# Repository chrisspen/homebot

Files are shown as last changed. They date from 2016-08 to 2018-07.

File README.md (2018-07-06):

Homebot
============================================================

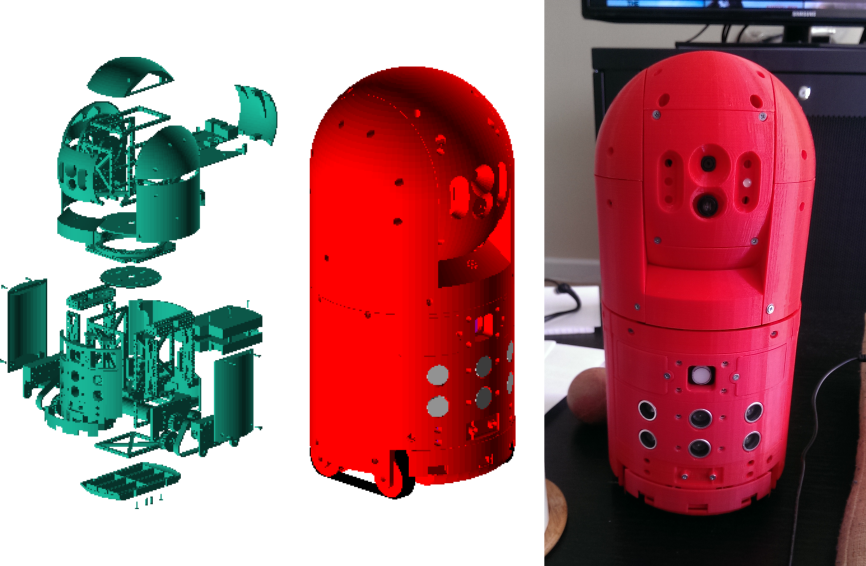
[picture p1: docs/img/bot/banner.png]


Homebot is a low cost open source robot designed for research and experimentation with [ROS](http://www.ros.org/).

Basic features include:

* head that can rotate 360 degrees horizontally and 180 degrees vertically
* monocular camera fitting with a laser ranger finder
* IMU with magnetic compass for navigation
* ultrasonic range finders and IR distance sensor for forward obstacle and cliff detection
* Raspberry Pi 3 for running ROS and high-level control
* charging dock

Demo:

[Undocking And Docking](https://youtu.be/g7_KL-V0nWs)

Shortcuts:

To deploy all code changes to the production robot, run:

    fab prod deploy.push

To just quickly push up Python code changes, run:

    fab prod homebot.deploy_code

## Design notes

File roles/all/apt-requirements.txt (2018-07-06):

# Install with:
# fab local packager.install_apt:roles/all/apt-requirements.txt

# Python
python-dev
python-pip
python-virtualenv

dphys-swapfile
#linux-firmware#not found on raspbian?
openssh-server
network-manager
wireless-tools
rsync

# Debugging helpers.
htop
curl
screen
git

# Needed by numpy/scipy
libatlas-base-dev
gcc
gfortran
g++
libblas-dev
liblapack-dev
gfortran

# Speech output.
espeak
alsa-utils
mpg321
lame

# Needed by cv2.
libgles2-mesa
libgles2-mesa-dev

# Needed by some packages that are built from source.
python-wstool
python-rosdep
ninja-build

# Needed by tf/robot-state-publisher.
libtf2-*

#ros-kinetic-robot-upstart

# Needed by Arduino firmware.
arduino-mk

# Needed by teleop and raspicam.
ros-kinetic-image-view
ros-kinetic-xacro
ros-kinetic-robot-state-publisher
ros-kinetic-rospy
ros-kinetic-compressed-image-transport
#libcamera-info-manager0d
#libcamera-info-manager-dev
ros-kinetic-camera-info-manager
libopencv-calib3d-dev

# Needed by homebot_description.
ros-kinetic-diagnostics
#ros-kinetic-diagnostics-msgs
ros-kinetic-robot-model

# Needed for raspicam
g++-arm-linux-gnueabihf

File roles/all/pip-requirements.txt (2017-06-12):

burlap==0.9.2

# Allows us to create GTK3 applications.
pgi==0.0.11.1

# head_arduino_tester
pyserial==3.2.1
#urwid==1.3.1

catkin-pkg==0.2.10

# Needed by system_node.py
# Note, large packages like scipy/numpy take forever to build on the RPi,
# so we install via the --only-binary option. However, the available versions
# with this option are limited, so we don't specify version.
#scipy==0.19.0
scipy
humanize==0.5.1
#numpy==1.12.0
numpy

#Fabric==1.10.2
#PyYAML==3.11
#burlap

#DEPRECATED: Installed by ROS?
#wiringpi2==1.1.1

Pillow==2.3.0
picamera==1.10

pint==0.7.2

# Required by ros_homebot_lrf.
#laser_range_finder
#-e git://github.com/chrisspen/laser-range-finder.git#egg=laser_range_finder

# Needed for ROS message generation.
empy==3.3.2

defusedxml
rospkg

# Teleop
Django==1.9.2
-e git://github.com/chrisspen/gevent-socketio.git#egg=gevent-socketio

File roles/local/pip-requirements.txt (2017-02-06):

# Needed by imu_visualizer.py.
vispy==0.4.0

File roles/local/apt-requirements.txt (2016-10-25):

# Needed by imu_visualizer.py.
libglfw3*

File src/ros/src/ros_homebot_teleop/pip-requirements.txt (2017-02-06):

Django==1.10.5
#gevent-socketio==0.3.6
#-e git+https://github.com/abourget/gevent-socketio.git#egg=gevent_socketio-dev
-e git://github.com/chrisspen/gevent-socketio.git#egg=gevent-socketio

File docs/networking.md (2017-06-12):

Networking
==========

Both wired and wireless connections are managed by Network Manager.

The wired connection will automatically be enabled when an ethernet cable is connected.

Wireless requires some setup, requiring an initial wired connection. Attached an ethernet cable and then confirm you can SSH in via:

    fab prod shell

Exit the shell, and setup the wireless connection by running:

    fab prod nm.add_wifi_connection:<SSID>,<PASSPHRASE>

If you get an error saying " No network with SSID '<SSID>' found." then list all available wireless networks by running:

    nmcli dev wifi list

If none are listed, then that indicates there might be a problem with the wireless driver.

Ensure all your packages and firmware is up-to-date by following [these instructions](https://raspberrypi.stackexchange.com/questions/44253/raspberry-pi-3-isnt-finding-wifi-networks).

    sudo apt-get update
    sudo apt-get upgrade
    sudo apt-get dist-upgrade
    sudo rpi-update
    sudo reboot

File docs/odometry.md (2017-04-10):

Odometry
========

Odometry measures the robot's translation and rotation from an arbitrary reference point. This is information necessary for planning robot movements and doing higher level actions like mapping and path planning.

Testing
-------

To confirm the robot is generating correct [odometry messages](http://docs.ros.org/api/nav_msgs/html/msg/Odometry.html), first start nodes to control the torso and visualize the robot:

    roslaunch ros_homebot_base serial_torso.launch
    roslaunch ros_homebot_description display_real.launch

Then command the motors to move foward are quarter speed using the differential format:

    rostopic pub --once /torso_arduino/motor/speed std_msgs/Int16MultiArray "{layout:{dim:[{label: '', size: 0, stride: 0}], data_offset: 0}, data:[64, 64]}"

or Twist format, which units are in meters:

    rostopic pub -1 /torso_arduino/cmd_vel geometry_msgs/Twist -- '[0.0875, 0.0, 0.0]' '[0.0, 0.0, 0.0]'

Note about speeds that the Arduino represents speed internally as an integer value between -255 to +255. A negative value is reverse. A positive value is forward. A zero value is stationary. To set speed via a Twist message, which only uses meters, the meter value has to be converted to the internal integer value. This is done in Motioncontroller.h via the `VELOCITY_TO_SPEED` ratio, which represents a conversion from a literal meter/second velocity value to a relative integer velocity value.

This value is about 728.57, and was determined by empirical measurement. However, it can vary based on nuances in the motor, motor controller, and tread friction with the ground.

To convert meters to integer value, you'd calculate `VELOCITY_TO_SPEED*METERS = SPEED`.

To convert an integer value to meters, you'd calculate `METERS = SPEED/VELOCITY_TO_SPEED`.

Since the maximum relative speed is 255, that means the maximum absolute speed is `255/728.57` = 0.35 meters/second.

Now look at the Rviz screen. If your motors are running and odometry messages are being generated correctly, you should see the robot moving forward in Rviz.

If you don't see anything, you'll need to diagnose the problem. Start by confirming odometry messages are being sent with:

    rostopic echo /torso_arduino/odom

If the robot is correctly shown to be moving, stop the robot with:

    rostopic pub --once /torso_arduino/halt std_msgs/Empty

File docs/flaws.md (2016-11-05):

Flaws
=====

This is a list of known design flaws.

1. battery charger overcharges

    If the battery pack is left connected while the robot is connected to external power, the LinkMan 2S-3S Lipo Balance Charger trickle charges the lipo until dangerously overcharged. Testing found that the 7.4V battery was overcharged to 8.9V, causing the battery to swell.
    
    Future designs should modify the recharge board to include a transistor that allows disconnecting the charger from the battery once the voltage reaches a safe storage voltage of 7.4V.
    
    This is really caused by the larger problem of our use of LiPo batteries. We're essentially trying to use the LiPo like an uninterruptible power supply, which means we try to keep the battery fully charged at all times. However, unlike Lead Acid batteries, used in most UPSes, which like to be kept fully charge, LiPo batteries tend to deterioate if kept at their full voltage for a few days.
    
    Workaround: When the robot is connected to external power, the battery should be charged to a safe storage charge of 7.4V and then removed.
    
    Effect: serious
    
2. limited expansion

    The overall footprint was kept small (15cm^2) to minimize cost and 3d printing time.
    However, even with use of small electronics, like the Arduino and Raspberry Pi, this leaves very little room for expansion and wire routing.
    
    Future designs should double this footprint.
    
    The motors and battery currently selected should still be powerful enough to actuate that size.
    
    Effect: average

3. front-panels are difficult to access

    The front panels, such as the bumper/edge sensor array, recharging dock, ultrasonic sensor array, and powerbutton, were designed as mainly a single piece, with electronics mounted behind, and then the entire assembly screwed onto the frame. This is difficult to access for maintainence because the panels can't easily be removed without also removing the wire connections to the Arduino. And in order to remove those, the head must be removed.
    
    Future designs should make enough room so wire slack can be added so the panels can be removed, or a socket used so the panel's electrical connections don't need direct wiring.
    
    Effect: average

4. battery charger discharges battery when load is off and external power is absent

    This is caused by the charger drawing current through the 3-pin balanced charging cable

    Future designs should add a diodes to ensure current only goes to the battery, back into the charger.

    Workaround: When the robot is turned off and disconnected from external power, the battery should be removed.
    
    Effect: average

5. treads lack suspension

    The treads ends are too blunt to overcome some sharp obstacles like door thresholds, without subjecting the robot to extensive shock.
    
    Future designs should raise the main idlers up, and include smaller more inset idlers, to allow suspension to dampen shocks.

    Workaround: place ballast in the bottom panels
    
    Effect: average

6. jittery head tilt

    The servo used to tilt the head up and down has considerable jittery, due to either a poor servo, or inadequate shielding along the servo control cable.
    
    Effect: average

7. inconsistent head pan reference sensor

    The sensor used to mark a centered head position is an IR sensor detecting a white reflective strip. This leads to false positives if there's considerable ambient light.
    
    Future designs should either use IR interruptor switch or hall effect sensor.
    
    Effect: minor

8. inadequate restraint in head side panels

    The two head neck struts are mechanically attached to the center head box via the servo spline on one side and a small clamp on the other. This allows for considerable play between the side head panels and the center head panels, creatign several mm of gap.
    
    Future designs should add small sliding retaining clasps, that attach to the corners of the head box and loop over the edge of the neck struts.

    Effect: minor

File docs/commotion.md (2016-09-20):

Prepare the ComMotion
---------------------

1. Mount the Commotion shield onto an Arduino, and plug the Arduino into a PC.
2. Install the i2cscanner Arduino sketch.
3. Confirm that it shows the address 0x1E (decimal 30) for the Commotion. If it does not, unplug the Arduino and change the Commotion's DIP switch to set the correct address. In my experience, most Commotion boards come configured for address 0x00 by default. Flip all DIP switches so they're closest to the numbers "1 2 3 4" to use the correct address.
4. Attach a short across the RST jumperr.

Prepare the Arduino
-------------------

1. Flash the "Arduino ISP" to the Arduino.

Upload ComMotion firmware
-------------------------

1. Use "File->Upload Using Programmer" option to upload firmware to the ComMotion through the Arduino Uno. THIS IS CRITICAL. USING THE NORMAL **UPLOAD** BUTTON WILL NOT WORK.

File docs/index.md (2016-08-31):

Introduction
============

Homebot is an affordable open source home-built robot designed for experimentation.

<span style="background-color: #FFFF00">This project is in beta status. Much of the documentation is incomplete.</span>

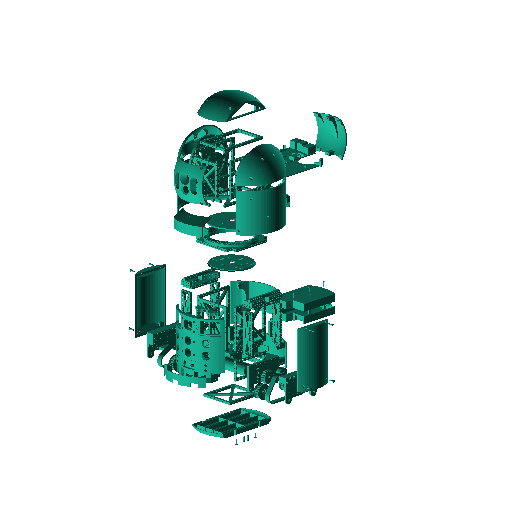
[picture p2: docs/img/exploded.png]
Exploded


#Disclaimer

This package is free software; the copyright holder gives unlimited permission to copy and/or distribute it, with or without modifications, as long as this notice is preserved. This package is distributed in the hope that it will be useful, but WITHOUT ANY WARRANTY, to the extent permitted by law; without even the implied warranty of MERCHANTABILITY or FITNESS FOR A PARTICULAR PURPOSE. Some information described herein may be potentially dangerous if misused. Follow these instructions are your own risk.

#Philosophy

This project has been constructed with the following philosophies in mind:

1. Openness
 
    There are several other "open source" robotics projects, but most only open source some of the software. Usually, large portions of the software are propreitary and most, if not all, of the hardware is proprietary. All of this project's software is open source and uses [ROS](http://www.ros.org/) as the framework. Most of the hardware is open source as well. The CAD files for all structural components are provided, and the core electronics are based on open hardware like the Raspberry Pi and Arduino. However, due to time and resource constraints, some propreitary off-the-shelf components were used.<br/><br/>

2. Modularity

    The mechanical design is based on modular components attached to a basic skeleton. Parts can be swapped out or redesigned and replaced without necessarily redesigning other components. 

#Features

The default hardware configuration is composed of:

* 1 Raspberry Pi 3 functioning as the main computer
* 2 Arudino microcontrollers for IO expansion and handling

Sensors include:

* 3 edge/cliff sensors
* 3 contact/bumper sensors
* 3 ultrasonic range finders
* 1 IMU (combined acclerometer, gyroscope and magnetometer)
* 2 microphones
* 1 5MP camera configured as a laser range finder with a functional distance of 3 meters
* 2 temperature sensors

A simple web-based user-interface is provided for operating the robot remotely and monitoring system status.

#Prerequisites

Although great effort has been made to make these instructions clear and the design as simple as possible, constructing a robot is complicated and requires a wide breadth of knowledge. This documentation assumes you have basic experience in:

* Mechanics

    You should have an understanding of basic physics, as well as how to assemble simple mechanical components. If you passed highschool physics and can assemble Ikea furniture, you should be set.<br/><br/>

* Electronics

    You should be able to read basic electricial circuit schematics, and how to wire, solder and etch simple circuit boards.<br/><br/>

* Software

    You should have an intermediate understanding of Python and C programming as well as basic network, database and Linux systems adminstration.<br/><br/>

#Onward!

1. [Allocate the appropriate tools](tools.md)
2. [Allocate the appropriate parts and supplies](parts.md)
3. [Setup your work environment](setup.md)
4. [Fabricate and assemble the hardware](hardware.md)
5. [Configure and test the software](software.md)
6. [Experiment](experiment.md)

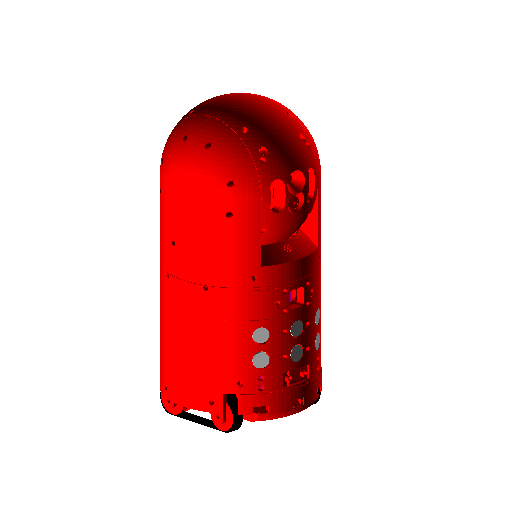
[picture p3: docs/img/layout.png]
Layout


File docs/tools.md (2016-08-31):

General
-------

To complete this project, you will need the following tools:

* a good phillips head screwdriver

    I recommend a gyroscopically controlled electric screwdriver, since it will allow fast assembly while still allowing you to regulate speed to prevent stripping.
    
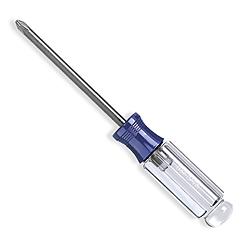
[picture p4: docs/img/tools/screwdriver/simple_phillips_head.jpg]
tool
    
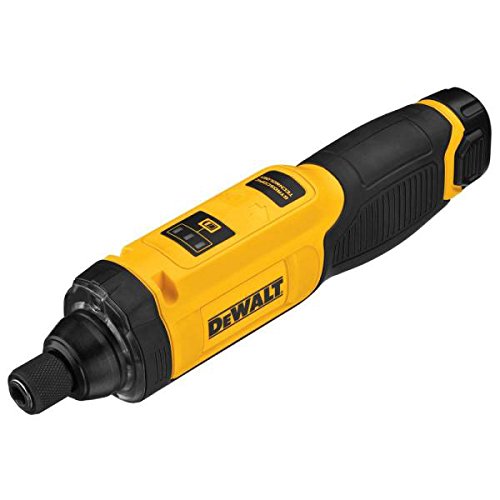
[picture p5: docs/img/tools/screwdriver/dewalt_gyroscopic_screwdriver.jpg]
tool
    
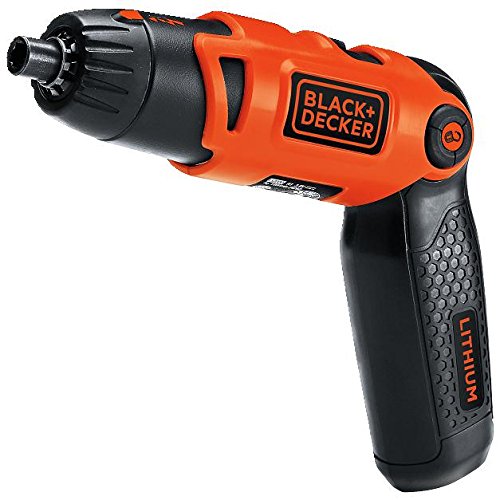
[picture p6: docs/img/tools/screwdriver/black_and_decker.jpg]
tool
    

* wire strippers

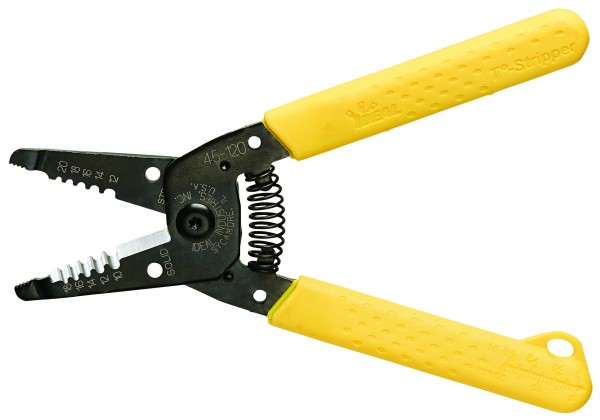
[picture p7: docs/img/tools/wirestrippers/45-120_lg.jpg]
tool
    
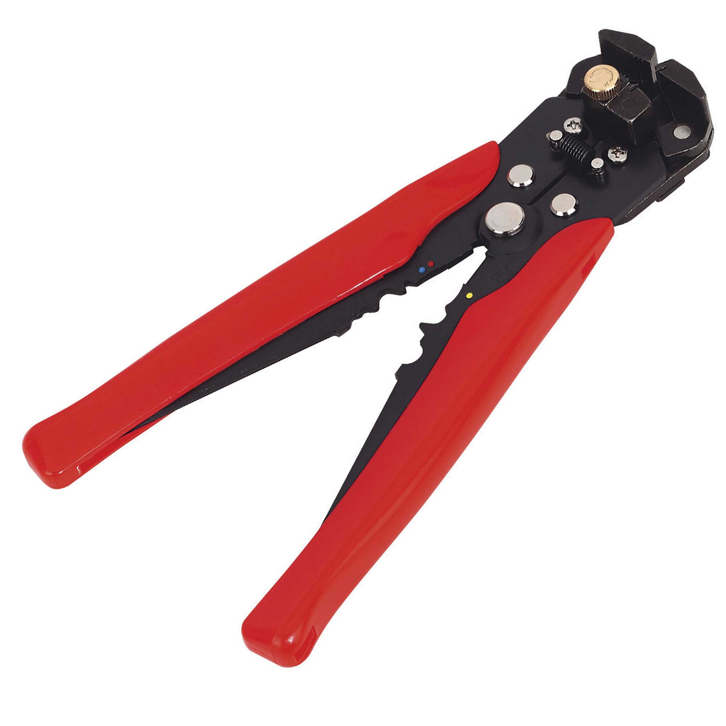
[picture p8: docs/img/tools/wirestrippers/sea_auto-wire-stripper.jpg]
tool
    

* flush wire cutter

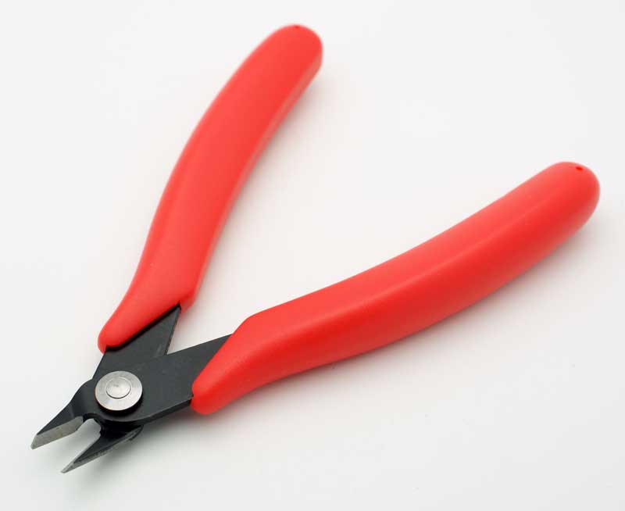
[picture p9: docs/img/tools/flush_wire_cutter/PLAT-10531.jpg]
tool
    

* exacto knife

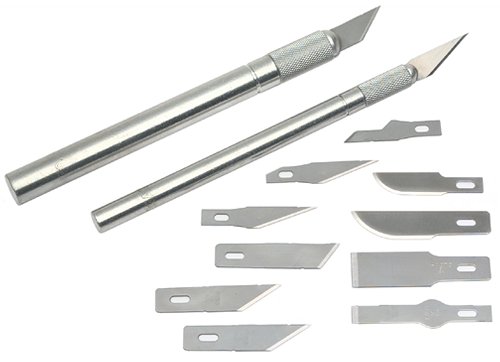
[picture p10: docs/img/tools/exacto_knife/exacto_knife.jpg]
tool
    
    
* tweezers

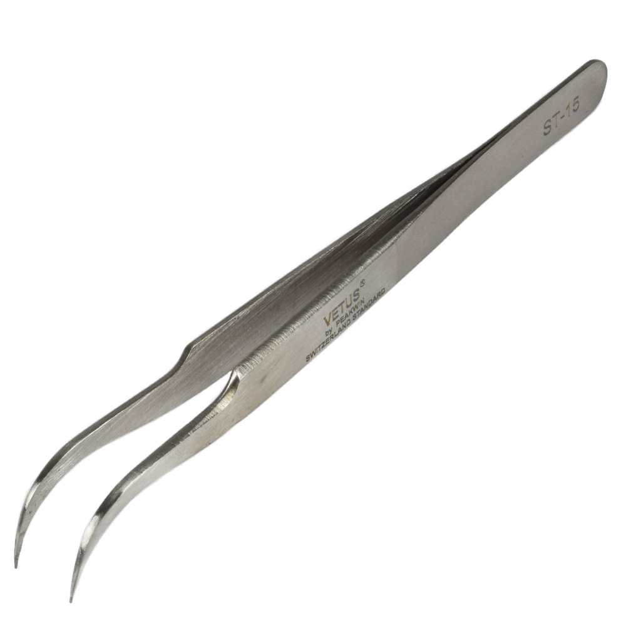
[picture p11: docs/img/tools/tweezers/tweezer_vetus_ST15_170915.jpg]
tool
    

* soldering iron

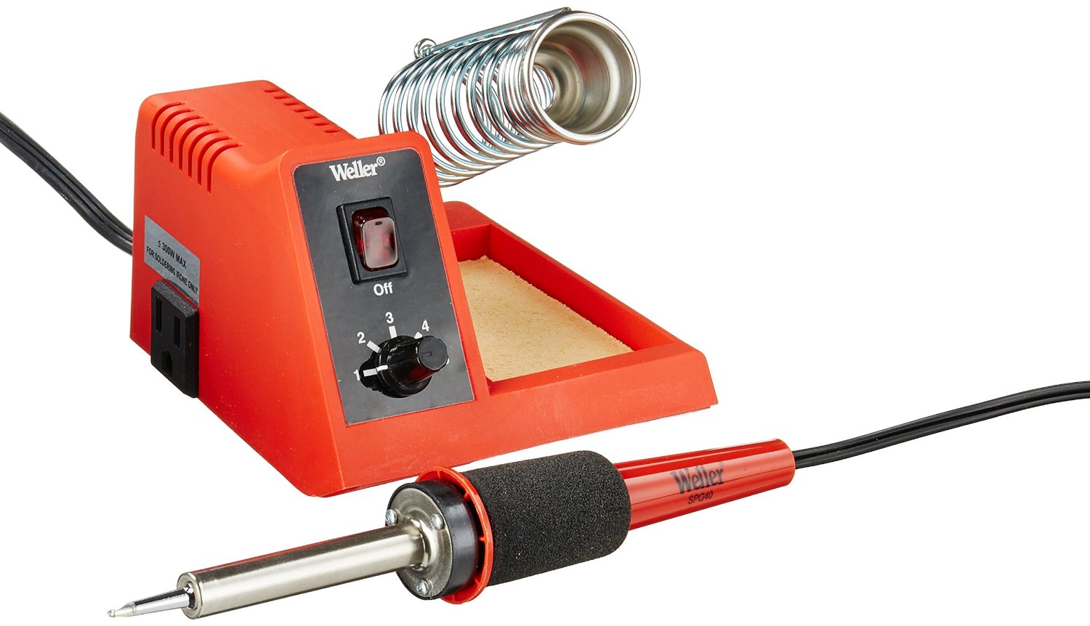
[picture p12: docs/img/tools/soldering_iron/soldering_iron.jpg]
tool
    

* helping hands

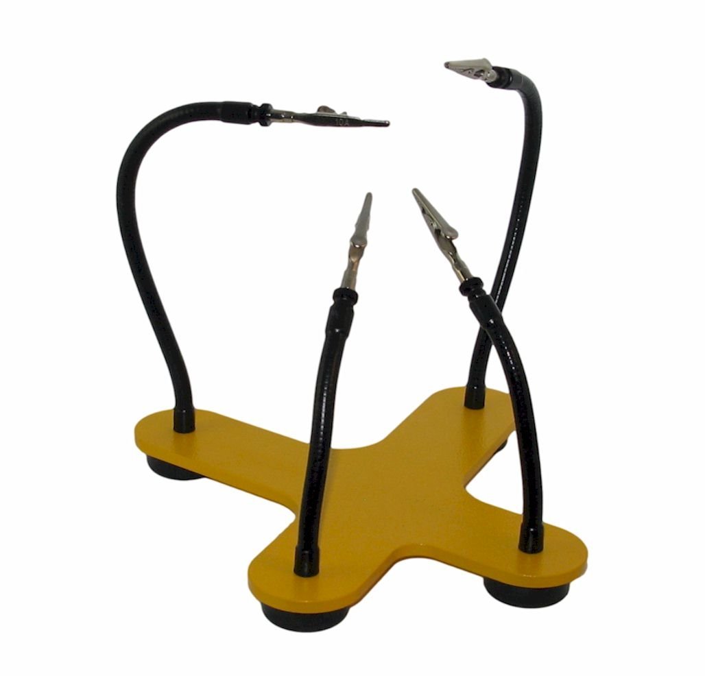
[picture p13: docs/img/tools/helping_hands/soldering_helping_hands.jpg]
tool
    

* heat gun

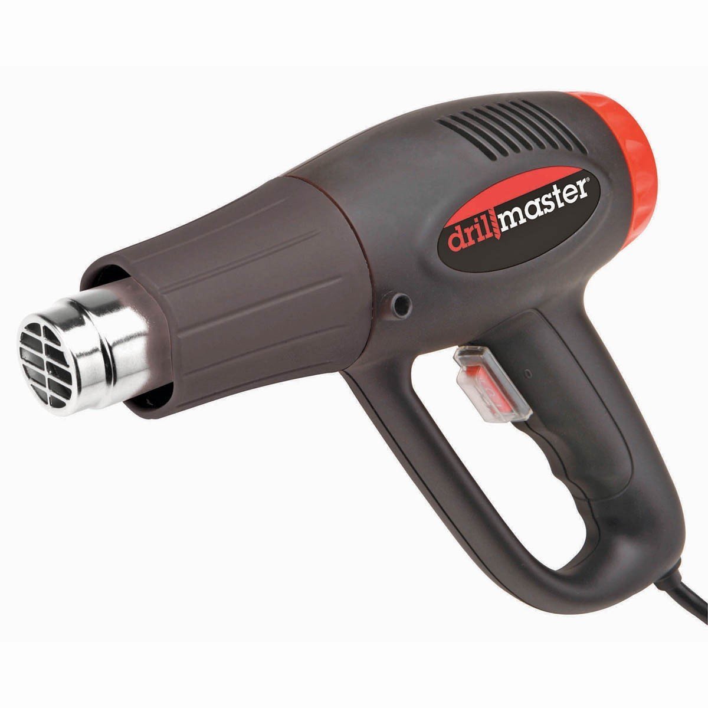
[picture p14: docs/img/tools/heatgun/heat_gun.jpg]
tool
    

3D Printing
-----------

If you want to 3D print the mechanical components yourself, you'll also need the following tools. If don't want to invest in a 3D printer, you can outsource the printing to one of many companies like [Shapeways.com](http://www.shapeways.com) or [Ponoko.com](Ponoko.com). 

* a 3d printer with a print volume of at least 15cm^3. All parts were originally developed and printed using a [Printrbot Simple Metal with heated bed](https://printrbot.com/shop/assembled-simple-metal-with-heated-bed/).

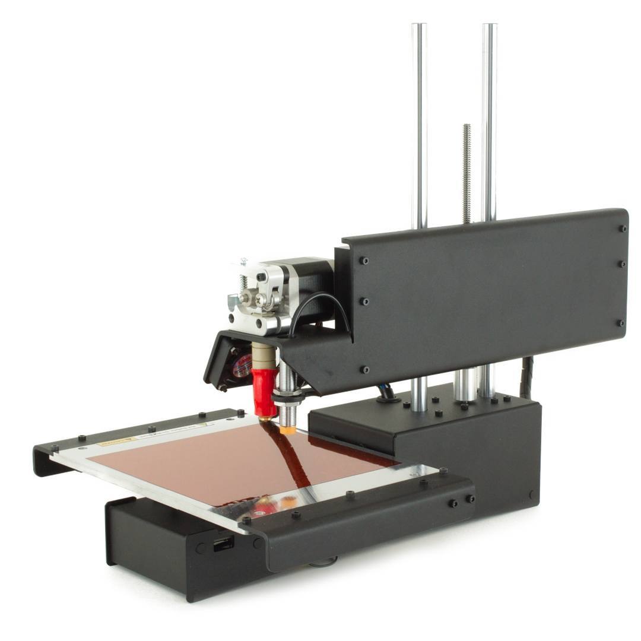
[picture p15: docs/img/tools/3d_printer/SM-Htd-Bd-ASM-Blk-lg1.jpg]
tool
    
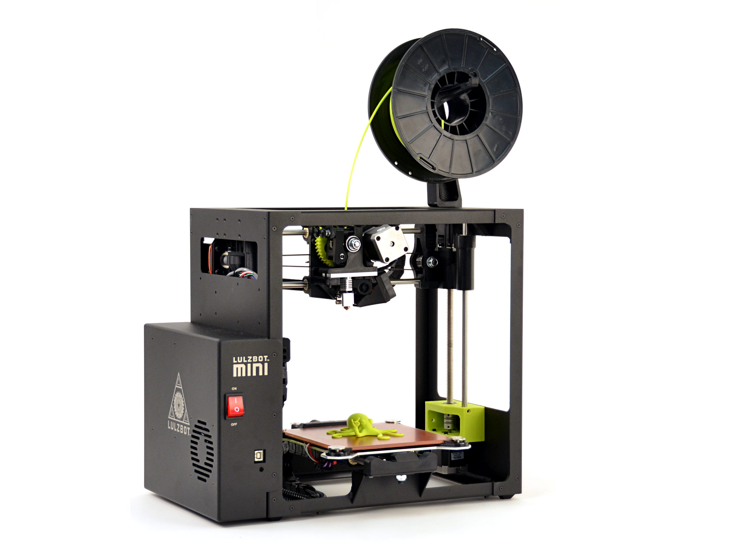
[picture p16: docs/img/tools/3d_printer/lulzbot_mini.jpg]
tool
    
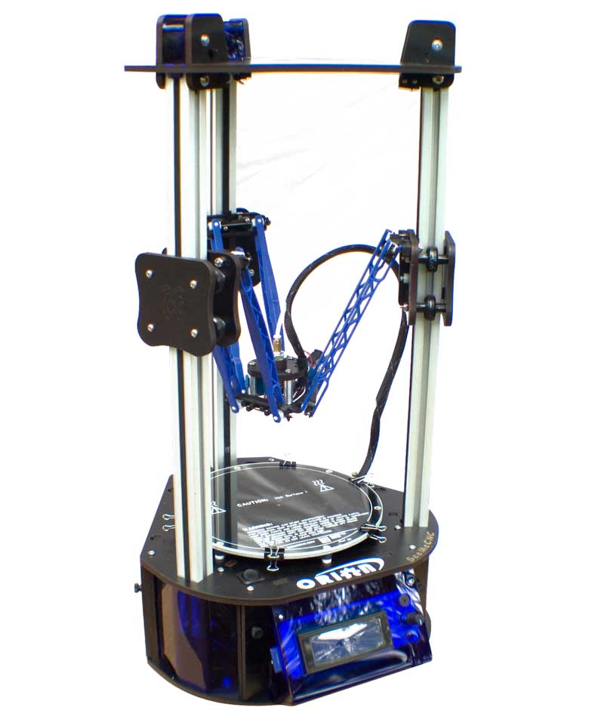
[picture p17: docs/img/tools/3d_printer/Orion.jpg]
tool
    

* 4-inch taping knife 

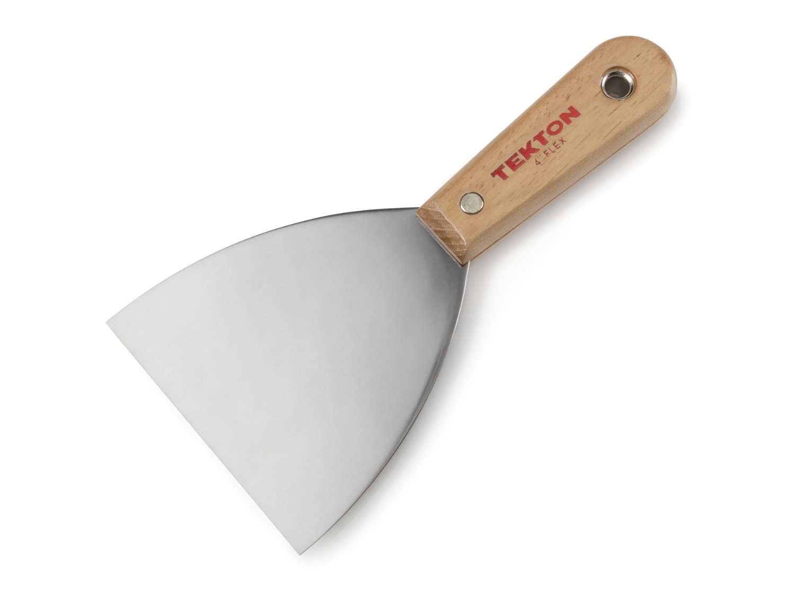
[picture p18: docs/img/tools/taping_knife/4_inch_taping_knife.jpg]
tool
    

* tapered pallet knife

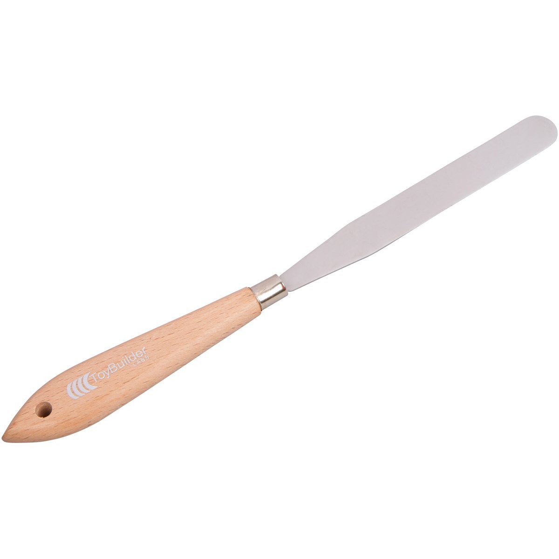
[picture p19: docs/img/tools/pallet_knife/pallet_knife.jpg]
tool
    

PCB Fabrication
---------------

If you plan to fabricate your own printed circuit boards, you'll need the additional tools.

* black and white laser printer

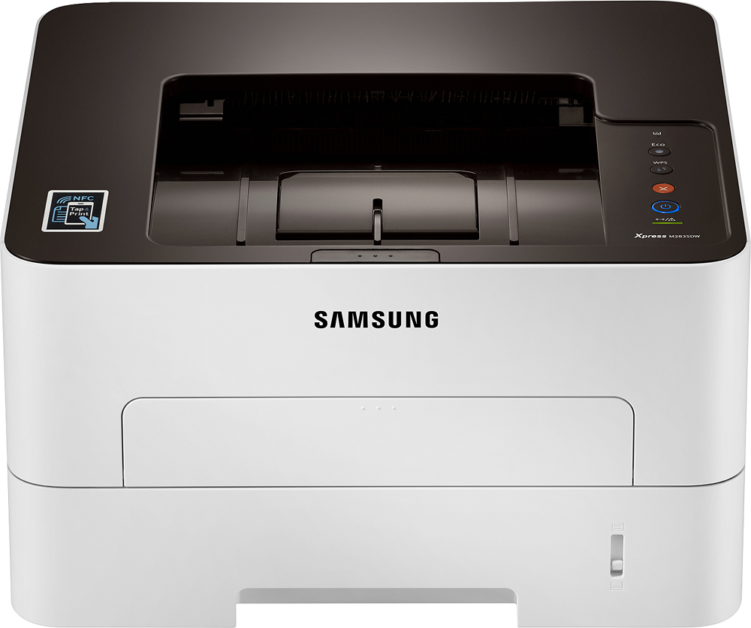
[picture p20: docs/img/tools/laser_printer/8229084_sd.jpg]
tool
    

* 1qt plastic container

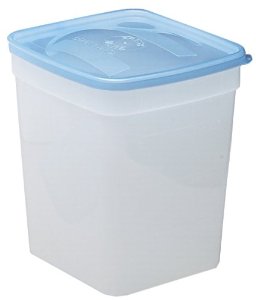
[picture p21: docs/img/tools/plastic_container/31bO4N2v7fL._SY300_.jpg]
tool
    

* air pump with bubbler

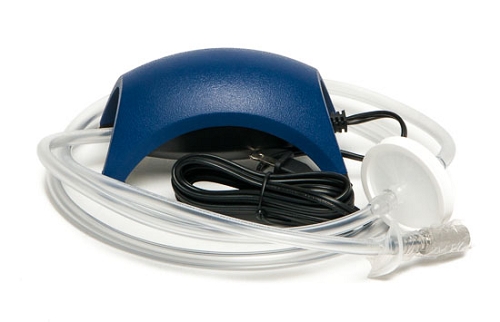
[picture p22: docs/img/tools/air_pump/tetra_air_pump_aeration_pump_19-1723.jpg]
tool
    
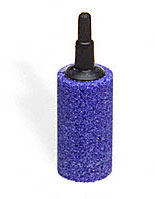
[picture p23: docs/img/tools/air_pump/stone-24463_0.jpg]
tool
    

* laminator

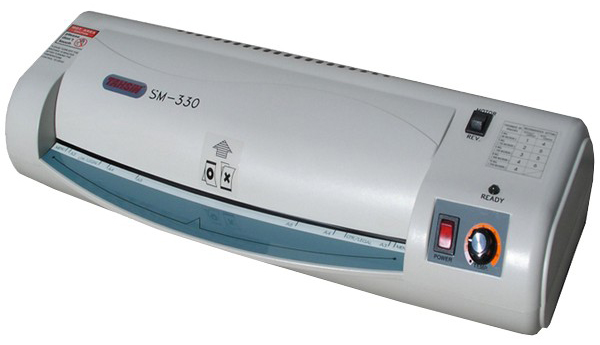
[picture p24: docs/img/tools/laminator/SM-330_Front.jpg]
tool
    

* toaster oven or reflow oven

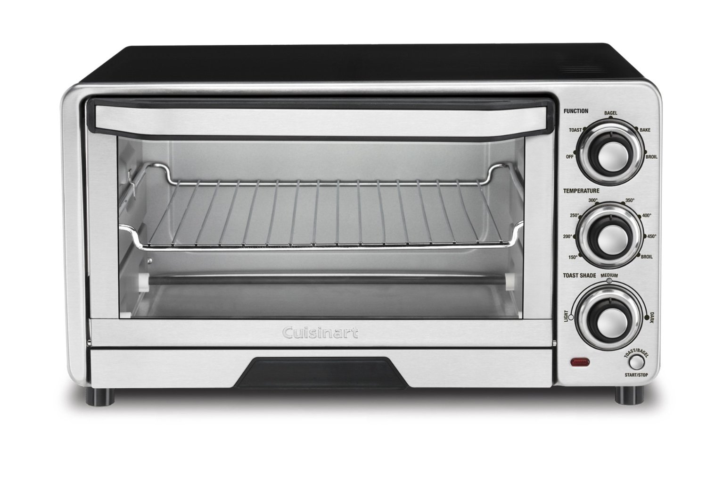
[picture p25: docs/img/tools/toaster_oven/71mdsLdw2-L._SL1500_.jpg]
tool
    
    tool

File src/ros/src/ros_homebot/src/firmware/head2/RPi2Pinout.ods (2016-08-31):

RPi2 Pin | GPIO Pin | Supports PWM | Mode | Function | Label | Wire Color | Notes
1 | 3.3V
2 | 5V
3 | I2C SDA
4 | 5V
5 | I2C SDL
6 | GND
7 | GPIO4
8 | NA
9 | GND
10 | NA
11 | GPIO17
12 | GPIO18
13 | GPIO27
14 | GND
15 | GPIO22
16 | GPIO23
17 | 3.3V
18 | GPIO24
19 | SPIO MOSI
20 | GND
21 | SPIO MISO
22 | GPIO25
23 | SPIO SCLK
24 | SPIO CS0
25 | GND
26 | SPIO CS1
27 | NA
28 | NA
29 | GPIO5
30 | GND
31 | GPIO6
32 | GPIO12
33 | GPIO13
34 | GND
35 | GPIO19
36 | GPIO16
37 | GPIO26
38 | GPIO20 |  | output | laser power | LP
39 | GND
40 | GPIO21

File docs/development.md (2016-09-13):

These are some miscellaneous notes and conventions about project development.

Creating New Messages and Actions
---------------------------------

Homebot fully supports the ROS concepts of [messages](http://wiki.ros.org/Messages), [services](http://wiki.ros.org/Services) and [actions](http://wiki.ros.org/actionlib).

Each of these is defined by a simple text file. Custom homebot-specific messages and services are defined in the ros_homebot_msgs package.

Many of the messages and services concerning the Arduino boards have been auto-generated by the ros_homebot_python package. The definitions for these are contained in `ros_homebot_python/constants.py`. If you ever add or modify this file, execute it with:

    python constants.py

Additional message and service definitions can be added to ros_homebot_msgs directly. If you do add new definitions, be sure to execute:

    python update_makelists.py

to ensure the ROS makelist contains the most recent list of messages and services to generate. Then, to rebuild all message and service objects, from the `src/ros` directory, run:

    . ./setup.bash
    catkin_make --pkg ros_homebot_msgs

Documentation Server
--------------------

To run the [documentation server](http://www.mkdocs.org/#getting-started) locally:

    mkdocs serve -a :9999

To [deploy documentation](http://www.mkdocs.org/user-guide/deploying-your-docs/), run:

    mkdocs gh-deploy --clean

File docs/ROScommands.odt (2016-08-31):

ROS Commands and Terminology

- rospack list – list all installed ROS packages
- rospack find <package-name> - find the package-name
- roscd <package-name> – change to this package’s directory (don’t need to be in the parent)
- rosls <package-name> – list the contents of the directory for this package
- roscore – start the ROS master
- node – a running instance of a program is called a node
- rosrun package-name executable-name --- start a node, rosrun doesn’t need a path to the executable; it infers the path to the executable from the package-name
- rosnode list – list all currently running nodes. Note: node names may not match the name of the executable.
- rosnode info – all sorts of useful info about the node
- rqt_graph – show the communication graph. Ovals represent nodes, arcs represent (and are labeled with) topics. Here you can see what topics are available (for publishing or subscribing) for your own programs.
- rostopic list – get a list of active topics
- rostopic echo topic-name – see the data that is being published on this topic (e.g., rostopic echo turtle1/pose)
- rostopic info topic-name – get a bunch of info about a topic. Note: first line tells the message type for the topic
- rosmsg show message-type-name – show details about the message type (i.e., show the names and data types of the components of the message).
- rostopic pub –r rate-in-hz topic-name message-type message-content – publish a message from the command line
- message type names always are of the form package-name/type-name (e.g., turtlesim/Pose)



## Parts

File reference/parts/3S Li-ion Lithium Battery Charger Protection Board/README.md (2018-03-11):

XINY 3S Li-ion Lithium Battery Charger Protection Board
=======================================================

https://www.amazon.com/XINY-Protection-Over-discharge-Overcurrent-Short-circuit/dp/B01J9BSJ80/

overcharge detection voltage :4.25 ± 0.025V(Stop charging, When 1 of 3 battery out voltage> 4.25 ± 0.025V)
over discharge detection voltage :2.50 ± 0.08V(Stop out, When 1 of 3 battery out voltage < 2.5V)
Operating Current: 15A (natural cooling 10A, additional heat sink 15A, the maximum instantaneous current of 30A)
Main features: over charge protection, over-discharge protection, short circuit protection, overcurrent protection.
No part design on the back, can be attached to the heat sink to ensure that large currents to work long hours.

Lift Condition: Protecting release the auto recovery, without activation.

Module:3S Li-ion Lithium Battery Protection Board
overcharge detection voltage :4.25 ± 0.025V
overcharge Lift the voltage:4.15 ± 0.05V
over discharge detection voltage :2.50 ± 0.08V
over discharge Lift the voltage:3.00 ± 0.1V
overcurrent current:20-30A
working current:15A(Natural cooling 10.A, add heat sink 15A, the maximum instantaneous current 30A)
Remove protection condition automatic recovery, without activation
Protections:
Short circuit protection
Overcharge protection
Over-discharge protection
Overcurrent protection
Operating temperature:-40~+85℃
Size:50*22*4mm(L*W*H)
Package include:
1 x 3S Li-ion Lithium Battery Charger Protection Board

DOES NOT BALANCE

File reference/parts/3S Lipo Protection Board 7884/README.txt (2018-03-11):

12.6V 4A 3S Dual MOS Polymer Li Battery Protection Board for 3pcs 18650
=======================================================================

http://www.icstation.com/126v-dual-polymer-battery-protection-board-3pcs-18650-p-7884.html

Icstation 12.6V 4A 3S Lithium Battery Protection PCB BMS Board With AO8810 Dual MOS for 18650 18550 Li-ion Lipo Battery Cell Pack

1. Input voltage:0-26V
2. Working temperature:-40~85℃
3. Overcharge protect voltage:4.325V-4.375V
4. Overcharge release voltage:4.1V-4.2V
5. Over discharge protect voltage:2.32V-2.48V
6. Over discharge release voltage:2.9V-3.1V
7. Overcharge protect delay time:0.5-1.5S
8. Overcharge release delay time:50-150ms
9. Over current protect delay time:0.4-1.6ms
10. Resistance: 30mohm ~ 80mohm
11. Static current:1.8-14.2uA
12. Over current:8-12A
13. Working voltage:6-12.6V

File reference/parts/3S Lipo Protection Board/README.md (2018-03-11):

Icstation 12V 8A 3S Lithium Battery Protection PCB BMS Board for 18650 18550 Li-ion Lipo Battery Cell Pack Sqaure
=================================================================================================================

https://www.amazon.com/Icstation-12V-8A-3S-Protection/dp/B01LX8M9DK/

Product Features

    12V 8A 3 cell Li-ion battery charge discharge protection board with Japan battery control IC
    Overcharge protection voltage: 4.2v±0.025v
    Over-discharge protection voltage: 2.8V±0.1V
    Continuous Working Current: 8A
    PCB size: 53 X 18 X 3mm/2.09 X 0.71 X 0.12inch(L*W*H)

Product Description
    
    This 3 cell lithium ion battery protection board is equiped with Japan battery control IC with over charging, over discharging, over current and short circuit protection.
    It is perfect for li-ion lipo battery cell pack such as 18650,18550, 14500 avoiding the damage during charging or discharge then prolong their lifetime.

Specifications:

    1. PCB size: 53 X 18 X 3mm/2.09 X 0.71 X 0.12inch(L*W*H)
    2. overcharge protection voltage: 4.2v±0.025v
    3. Over-discharge protection voltage: 2.8v±0.1v
    4. Continuous Working Current: 8A
    5. Maximum Load: 90W@12V

Package Included:

    2X 12V 8A 3S 18650 Lithium Battery Protection Board

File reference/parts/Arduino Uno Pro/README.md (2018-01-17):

Arduino Uno Pro
===============

http://www.hobbytronics.co.uk/arduino-uno-pro

https://github.com/maniacbug/mighty-1284p

Arduino UNO*Pro - Upgrade

The UNO*Pro is a simple plugin replacement for the existing ATmega328 chip (DIL socket version) and turns your existing UNO (or Duemilanove or Diecimila) into something much closer to a Mega board whilst retaining the UNO form factor and shield compatibility (see below). NOTE: Arduino main board not included.

The Arduino UNO is still the best selling Arduino board on the market, and with good reason - there are a vast range of shields available for the UNO board format.

The UNO is still a great development board, but it loses out to its big brother the Arduino Mega2560 in many areas. The Mega has 4x the flash program space, 8x as much RAM and four times as much eeprom storage space. It also has 4 serial ports and many more IO pins, but comes in a larger format and a number of shields are not compatible due to pin changes. So how can you increase the performance of the Arduino UNO? This is where the UNO*Pro upgrade board comes in.

The UNO*Pro replaces your Arduino ATmega328/168 chip with an ATmega1284 chip

Shield Compatibility
--------------------

For the most part, the UNO*Pro should be compatible with most shields designed for the Arduino UNO.

What is the same as an Arduino UNO

    All the digital pins D0 through D13
    SPI pins (SCK, MISO, MOSI)
    Analog inputs A0 - A3
    I2C pins (SDA / SCL)

What has changed

    Some of the PWM pins have changed. PWM is no longer available on D5, D6 and D11. These PWM outputs have moved to D8, D12 and D13
    Analog inputs A4 and A5 are no longer on the same pins as the I2C pins. They are now available on the extra 12 way header

NOTE: The analog-to-digital (ADC) pins seem to behave a little differently. Using digitalRead() on these pins, a higher than usual reference voltage is used, resulting in even 4V being interpreted as a logical 0. If you want to get normal behavior, you'll need to use analogRead() and then convert that 0-1024 scale to 0-1.

Also, YOU CANNOT USE ANY OF THE ANALOG PINS AS OUTPUTS. They only work as inputs.

Installation
------------

Adding the UNO*Pro board to Arduino IDE

Before you can use your new UNO*Pro, you need to add support for the ATmega1284 chip to the Arduino IDE

Arduino 1.05 or below

If you are using Arduino 1.0.5 or below then download the Arduino ATmega1284 support files below and copy the atmega1284p directory into your arduino/hardware directory.

Arduino 1.5.5 and above

If you are using Arduino 1.5.5 or later then installation is simpler.

Under the hardware/arduino/avr/variants directory create a new directory called uno_pro

    In latest latest versions of the Arduino IDE it stores its settings in a different location
    For version 1.6.12 for example it will be something like
    C:\Users\________\AppData\Local\Arduino15\packages\arduino\hardware\avr\1.6.12\

Into this directory place the file pins_arduino.h

Next, open the hardware\arduino\avr\boards.txt file with a text editor and add the following entries for the UNO*Pro board

##############################################################

uno_pro.name=Arduino Uno*Pro

uno_pro.upload.tool=avrdude
uno_pro.upload.protocol=arduino
uno_pro.upload.maximum_size=130048
uno_pro.upload.maximum_data_size=16384
uno_pro.upload.speed=115200

uno_pro.bootloader.tool=avrdude
uno_pro.bootloader.low_fuses=0xFF
uno_pro.bootloader.high_fuses=0xDE
uno_pro.bootloader.extended_fuses=0xFD
uno_pro.bootloader.unlock_bits=0x3F
uno_pro.bootloader.lock_bits=0x0F
uno_pro.bootloader.file=optiboot/optiboot_atmega1284p.hex

uno_pro.build.mcu=atmega1284p
uno_pro.build.f_cpu=16000000L
uno_pro.build.board=AVR_UNO_PRO
uno_pro.build.core=arduino
uno_pro.build.variant=uno_pro

##############################################################

Programming the new UNO*Pro

Programming your upgraded UNO*Pro board is just the same as before using the normal Arduino IDE software. The only difference is that you need to select Arduino UNO*Pro rather than Arduino Uno from the Boards menu.

Start up the Arduino IDE and select Arduino UNO*Pro.

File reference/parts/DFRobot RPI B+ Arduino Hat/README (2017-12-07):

Raspberry Pi B+ Meet Arduino Shield SKU:DFR0327

http://www.dfrobot.com/wiki/index.php?title=Raspberry_Pi_B%2B_Meet_Arduino_Shield_SKU:DFR0327

https://www.dfrobot.com/wiki/index.php/Arduino_Shield_for_Raspberry_Pi_2B_and_3B_SKU:DFR0327

Specification

    Onboard Microcontroller: ATmega32u4
    Arduino Leonardo Chip
    Arduino Compatible pin mapping
    Compatible with All arduino standard shield and sensors
    System Voltage: 5v
    Arduino Digital I/O: 20
    Arduino Analog I/O: 6
    Raspberry Pi B+ GPIO : 16
    Raspberry Pi B+ I2C: 1
    Raspberry Pi B+ ID_I2C: 1
    Raspberry Pi B+ SPI: 1
    Raspberry Pi B+ TTL UART: 1
    Dimension: 88mm x 56mm x 26mm

Note, the Pi-ID IIC pins go to the RPi pins 27/28 (ID_SD/ID_SC), which is the I2C interface for the EEPROM.

The Pi-IIC pins go to the normal I2C pins at RPi pins GPIO2 (SDA) and GPIO3 (SCL).

Note of warning. This shield appears as an I2C device at address 0x68. This shouldn't be a problem in most cases, but make sure any I2C devices you want to use with it aren't hardcoded for that same address. Otherwise they won't work. I stumbled into this problem with an I2C device that also happened to use address 0x68.

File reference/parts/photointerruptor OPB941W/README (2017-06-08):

https://www.digikey.com/product-detail/en/tt-electronics-optek-technology/OPB941W51Z/365-1234-ND/1007365

Wiring (for a GVS sensor plug):

    Connect green (gnd) and black (cathode) wires together, this will be the common ground.
    
    Add a resistor of 330 in series with red (anode). This limits the current through the IR emitter.
    
    Connect white (vcc) to the anode resistor (red). This will be +5V.
    
    Leave blue (out) as is. This will be signal out, going to a digital pin on the Arduino, configured to use a 20k pullup resistor.

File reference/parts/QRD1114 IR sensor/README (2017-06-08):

Design 1:

    Pin 1 (IR receiver output) in series with resistor 25700. (white)
    
    Pins 2 and 4 connected to ground. (black)
    
    Pin 3 (IR emitter +V) in series with resistor 330. (red)

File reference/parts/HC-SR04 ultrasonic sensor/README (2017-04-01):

HC-SR04 ultrasonic sensor

Note, even though it has two pins for Trig and Echo, these can be shorted to create a three-pin interface.

https://bitbucket.org/teckel12/arduino-new-ping/wiki/Home#!examples

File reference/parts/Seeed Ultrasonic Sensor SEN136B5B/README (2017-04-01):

Seeed Ultrasonic Sensor SEN136B5B

http://wiki.seeed.cc/Ultra_Sonic_range_measurement_module/

Features:
    
    Detecting range: 3cm-4m 

    Best in 30 degree angle 

    Electronic brick compatible interface 

    5VDC power supply 

    Breadboard friendly

    Dual transducer 

    Arduino library ready

Specifications
    
    Supply voltage  5V
    Global Current Consumption  15 mA
    Ultrasonic Frequency    40k Hz
    Maximal Range   400 cm
    Minimal Range   3 cm
    Resolution  1 cm
    Trigger Pulse Width     10 μs
    Outline Dimension   43x20x15 mm

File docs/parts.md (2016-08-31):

#Parts

A complete list of parts, estimated prices, and suggested retail links is available [here](parts.ods).

#Supplies

* 3040 3M Blue Painter's tape

* acetone

* paper towels

* 1kg of red PLA filament

* 0.5kg of black PLA filament

* 0.5kg of black Ninjaflex filament

* 60/40 solder

#PCB fabrication supplies

If you plan to fabricate your own PCB, you'll need the additional supplies.

* white vinegar

* hydrogen peroxide

* non-iodized salt

* single side FR4 copper clad board

* PCB toner transfer paper

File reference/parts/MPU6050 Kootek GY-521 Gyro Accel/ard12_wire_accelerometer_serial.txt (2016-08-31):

// This example read 14 values from an MPU-6050 digital accelerometer/gyroscope,
// using the Wire library for Arduino. It sends these values over the serial line
// to a PC.
// These values are 6 bytes acceleration measurements, 2 bytes temperature
// measurement, 6 bytes gyroscope measurements.

#include<Wire.h>

const int address=0x68;              // I2C address of the MPU-6050 accelerometer

void setup(){
  // the following lines of code init the Wire library and wake-up the accelerometer
  Wire.begin();
  Wire.beginTransmission(address);   // speak with I2C address 0x68
  Wire.write(0x6B);
  Wire.write(0);
  Wire.endTransmission(true);
  // initiate serial communication with the PC
  Serial.begin(57600);
}

void loop(){
  Wire.beginTransmission(address);
  Wire.write(0x3B);                   // starting action at register 0x3B
  Wire.endTransmission(false);

  Wire.requestFrom(address,14,true);  // request values from 14 registers (0x3B .. 0x48)
  Serial.write('#');                  // ... and send them over the serial line
  Serial.write(Wire.read());          // ACCEL_XOUT_H
  Serial.write(Wire.read());          // ACCEL_XOUT_L
  Serial.write(Wire.read());          // ACCEL_YOUT_H
  Serial.write(Wire.read());          // ACCEL_YOUT_L
  Serial.write(Wire.read());          // ACCEL_ZOUT_H
  Serial.write(Wire.read());          // ACCEL_ZOUT_L
  Serial.write(Wire.read());          // TEMP_OUT_H
  Serial.write(Wire.read());          // TEMP_OUT_L
  Serial.write(Wire.read());          // GYRO_XOUT_H
  Serial.write(Wire.read());          // GYRO_XOUT_L
  Serial.write(Wire.read());          // GYRO_YOUT_H
  Serial.write(Wire.read());          // GYRO_YOUT_L
  Serial.write(Wire.read());          // GYRO_ZOUT_H
  Serial.write(Wire.read());          // GYRO_ZOUT_L
  delay(500);                         // wait 0.5 seconds
}

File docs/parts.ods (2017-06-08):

Name | Part Number | Partial Usage | Unit Price | Quantity | Total Price | Open | Notes | URL | Alternative
CONN RCPT 5POS 5.00MM PCB SLDR | A115298-ND |  | $6.41 | 1 | $6.41 |  | battery pins | http://www.digikey.com/product-detail/en/te-connectivity-amp-connectors/5146800-1/A115298-ND/2262232
CONN HDR 5POS 5.00MM KINKED PIN | 5787446-1-ND |  | $2.98 | 1 | $2.98 |  | battery receptacle | http://www.digikey.com/product-detail/en/te-connectivity-amp-connectors/5787446-1/5787446-1-ND/1122081
Arduino Uno |  |  | $25.00 | 1 | $25.00 | 1 | torso controller | Arduino Uno
Arduino Uno Pro expansion board | UNOPRO |  | $13.00 | 1 | $13.00 |  | torso controller | http://www.hobbytronics.co.uk/arduino-uno-pro
Raspberry Pi 3 |  |  | $35.00 | 1 | $35.00 | 1 | main computer | https://www.raspberrypi.org/products/raspberry-pi-3-model-b/
ComMotion Motor Controller | RS039 |  | $45.00 | 1 | $45.00 | 0 | Discontinued. | http://www.dagurobot.com/goods.php?id=174
BMS-706MG Servo |  |  | $16.00 | 1 | $16.00 |  | head tilt actuator | http://www.hobbyking.com/hobbyking/store/__8784__BMS_706MG_Low_Profile_High_Speed_Servo_Metal_Gear_4_6kg_13sec_32g.html
Turnigy nano-tech 3000mAh 2S2P |  |  | $18.00 | 1 | $18.00 |  | main battery | http://www.hobbyking.com/hobbyking/store/__23821__Turnigy_nano_tech_3000mAh_2S2P_20_40C_Lipo_Receiver_Pack.html
Andoer BEC UBEC 3A 5V regulator |  |  | $7.00 | 5 | $35.00 | 0 |  | http://www.amazon.com/Andoer-Receiver-Servo-Power-Supply/dp/B00NCLEPHI
Raspberry PI 5MP Camera |  |  | $17.00 | 1 | $17.00 |  |  | http://www.amazon.com/Raspberry-5MP-Camera-Board-Module/dp/B00E1GGE40
Miniature Slip Ring - 12mm diameter, 6 wires |  |  | $18.00 | 1 | $18.00 |  |  | https://www.adafruit.com/products/775
led push button |  |  | $2.00 | 1 | $2.00 |  |  | https://www.adafruit.com/products/1479
Adafruit Mono 2.5W Class D Audio Amplifier |  |  | $4.00 | 1 | $4.00 | 0 |  | https://www.adafruit.com/product/2130
Raspberry Pi B+ Meet Arduino Shield | DFR0327 |  | $22.00 | 1 | $22.00 | 1 |  | http://www.dfrobot.com/index.php?product_id=1211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
Line Laser Module <1mW | 03015L |  | $13.00 | 1 | $13.00 |  |  | https://www.apinex.com/ret2/03015L.html
Kootek GY-521 Gyro Accel |  |  | $6.00 | 1 | $6.00 | 0 |  | http://www.amazon.com/Kootek-MPU-6050-MPU6050-sensors-Accelerometer/dp/B008BOPN40
RGB led |  |  | $2.00 | 1 | $2.00 |  |  | https://www.sparkfun.com/products/105
Pololu 2282 Gear Motor |  |  | $35.00 | 2 | $70.00 |  |  | https://www.pololu.com/product/2282
Pololu Mini Pushbutton Power Switch |  |  | $4.00 | 1 | $4.00 | 0 |  | https://www.pololu.com/product/2808
Pololu 50:1 Micro Metal Gearmotor HP |  |  | $16.00 | 2 | $32.00 |  |  | https://www.pololu.com/product/998
DRV8838 Single Brushed DC Motor Driver Carrier |  |  | $4.00 | 1 | $4.00 | 0 |  | https://www.pololu.com/product/2990
Pololu Carrier with Sharp GP2Y0D805Z0F |  |  | $6.00 | 3 | $18.00 | 0 |  | https://www.pololu.com/product/1132
OPB941W51 |  |  | $6.00 | 1 | $6.00 |  |  | https://www.digikey.com/product-detail/en/tt-electronics-optek-technology/OPB941W51Z/365-1234-ND/1007365
Sensor Shield for Arduino Kit | SB-GVS |  | $14.00 | 1 | $14.00 | 1 | torso io | https://solarbotics.com/product/39230/
Box of 100 2mm x 0.4mm x 5mm phillips pan head machine screws | 17847 | 1 | $1.99 | 1 | $1.99 |  |  | https://www.boltdepot.com/Product-Details.aspx?product=17847
Box of 100 2.5mm x 0.45mm x 10mm phillips flat head machine screws | 17970 | 1 | $2.19 | 1 | $2.19 |  |  | https://www.boltdepot.com/Product-Details.aspx?product=17970
Box of 100 2.5mm x 0.45mm x 14mm phillips flat head machine screws | 17972 | 1 | $2.29 | 1 | $2.29 |  |  | https://www.boltdepot.com/Product-Details.aspx?product=17972
Box of 100 2.5mm x 0.45mm x 20mm phillips flat head machine screws | 17974 | 1 | $3.00 | 1 | $3.00 |  |  | https://www.boltdepot.com/Product-Details.aspx?product=17974
Box of 100 2.5mm x 0.45mm x 25mm phillips flat head machine screws | 17975 | 1 | $4.31 | 1 | $4.31 |  |  | https://www.boltdepot.com/Product-Details.aspx?product=17975
M2.5 Nylon Insert Lock Nuts....12 Pcs | ML025 |  | $2.45 | 1 | $2.45 |  |  | http://www.rtlfasteners.com/RC/ml025.html
Red 1.75mm PLA |  | 1 | $24.00 | 1 | $24.00 |  | doesn't have to be red | http://www.amazon.com/HATCHBOX-3D-PLA-1KG1-75-RED-Filament-Dimensional/dp/B00J0GO8I0
Black 1.75mm PLA |  | 1 | $24.00 | 1 | $24.00 |  | DOES have to be black | http://www.amazon.com/HATCHBOX-3D-PLA-1KG1-75-BLK-Filament-Dimensional/dp/B00J0ECR5I
Ninjaflex 1.75mm PLA |  | 1 | $44.00 | 1 | $44.00 |  |  | http://www.amazon.com/NinjaFlex-Filament-Diameter-Spool-Midnight/dp/B00TOOFIZA
SPEAKER 8OHM 1W 80DB | 668-1435-ND |  | $4.45 | 1 | $4.45 |  |  | https://www.digikey.com/product-detail/en/pui-audio-inc/AS01808MR-LW152-R/668-1435-ND/4835127
Right-angle type B male USB cable | USBR09-0004 |  | $7.05 | 1 | $7.05 |  |  | https://www.blackbox.com/store/us/Detail.aspx/Universal-Serial-Bus-USB-Cable---Version-2-0-Right-Angle-Type-B-Male-to-Type-A-Male-4-ft-1-2-m-/USBR09-0004 | http://www.digikey.com/product-detail/en/assmann-wsw-components/A-USBPB-2/AE11179-ND/5017726
USB 2.0 Type A Solder 4 Pin Male Plug Connector |  |  | $11.14 | 1 | $11.14 |  |  | http://www.amazon.com/uxcell®-55pcs-Solder-Connector-Socket/dp/B00X73KVKG/
2S Lipo protection board |  |  | $7.00 | 1 | $7.00 | 0 | Unused. | http://www.amazon.com/Protection-Circuit-Module-Li-ion-Battery/dp/B00N48RCS8
60W 12V 5A Adapter |  |  | $7.00 | 1 | $7.00 |  | Design flaw. | http://www.amazon.com/Replacement-Adapter-Charger-Benq-Monitors/dp/B003Z6ZR5O
led assembly |  |  | $2.49 | 1 | $2.49 |  |  | http://www.amazon.com/RadioShack-Assembly-Holder-Lead-Wires/dp/B00LENYJKE
2.5mm Diameter Chrome Steel Bearing Balls |  |  | $5.37 | 1 | $5.37 |  |  | www.amazon.com/Diameter-Chrome-Bearing-Bearings-VXB/dp/B004YL46YC
Inside Diameter: 6mm Outside Diamater: 10mm Width: 2.5mm ball bearing |  |  | $9.89 | 1 | $9.89 |  |  | http://www.amazon.com/MR106-10-2-5-Ball-Bearing/dp/B00GGQ2RVM
9.5mm (.375=3/8in) diameter, 3.1mm (.125=1/8in) thickness Neodymium magnet |  |  | $0.32 | 2 | $0.64 |  |  | http://appliedmagnets.com/neodymium-magnets-n50-3-8-in-x-1-8-in-rare-earth-disc-p-543.html
2 ft of 14 guage steel wire |  | 1 | $5.00 | 1 | $5.00 |  |  | http://www.amazon.com/s/?url=search-alias%3Daps&field-keywords=14+gauge+steel+wire
misc heat shrink tubing |  | 1 | $5.00 | 1 | $5.00 |  |  | http://www.amazon.com/s/?url=search-alias%3Daps&field-keywords=heat+shrink+tubing
right angle micro B USB cable |  | 1 | $8.00 | 1 | $8.00 |  |  | https://www.amazon.com/gp/product/B00MEYWJ6I/
3M Scotch 2090 4” width Blue Painter's Tape |  | 1 | $12.00 | 1 | $12.00
10 ft of 22 awg red, blue, white, black stranded wire |  | 1 | $5.00 | 1 | $5.00
10 ft of 24 awg red, blue, white, black stranded wire |  | 1 | $5.00 | 1 | $5.00
10 ft of 26 awg red, blue, white, black stranded wire |  | 1 | $5.00 | 1 | $5.00
 |  |  |  |  | $636.65

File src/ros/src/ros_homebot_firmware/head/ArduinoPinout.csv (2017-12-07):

Arduino Pin | Supports PWM | Supports Interrupt | Mode | Function | Label | Variable | Wire Color | Notes
D0 |  | 1 | NA | USB
D1 |  | 1 | NA | USB
D2 |  | 1 | I2C | SDA
D3 | 1 | 1 | I2C | SCL
D4 |  |  | output | pan motor phase | PPH | PAN_MOTOR_PHASE | blue
D5 | 1 |  | output | pan motor enable (pwm) | PEN | PAN_MOTOR_ENABLE | white
D6 | 1 |  | output | tilt servo position set (pwm) | TS | TILT_SERVO_POS_SET
D7 |  | 1 | input | pan motor encoder A | PEA | PAN_MOTOR_ENCODER_A | white
D8 |  |  | input | pan motor encoder B | PEB | PAN_MOTOR_ENCODER_B | gray
D9 | 1 |  | output | Ultrabright 1 | L1 | ULTRABRIGHT_LED_1
D10 | 1 |  | output | led blue | LB | STATUS_LED_BLUE | blue
D11 | 1 |  | output | led green | LG | STATUS_LED_GREEN | brown
D12 |  |  | output | Ultrabright 2 | L2 | ULTRABRIGHT_LED_2
D13 | 1 |  | output | led red | LR | STATUS_LED_RED | red
A0 |  |  | output | Ultrabright 3 | L3 | ULTRABRIGHT_LED_3 |  | bad? ADC failed for servo analogRead()
A1 |  |  | output | tilt servo position get | TG | TILT_SERVO_POS_GET
A2 |  |  | output | pan motor reference position | PGA | PAN_MOTOR_POSITION_REF
A3
A4
A5
head1

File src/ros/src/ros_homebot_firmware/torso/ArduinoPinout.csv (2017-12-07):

Arduino Pin | Supports Interrupt | Mode | Supports PWM | Function | Label | Label Color | Variable | Wire Color | Notes
D0 |  | NA |  | USB
D1 |  | NA |  | USB
D2 | 1 | input |  | accel/gyro interrupt | AGI |  | ACCEL_GYRO_INT_PIN
D3 | 1 | input | 1 | ultrasonic left | L | red | SONIC_L_PIN
D4 |  | input |  | ultrasonic middle | M | red | SONIC_M_PIN
D5 |  | input | 1 | ultrasonic right | R | red | SONIC_R_PIN
D6 |  | input | 1 | edge left | L | blue | EDGE_L_PIN
D7 |  | input |  | edge middle | M | blue | EDGE_M_PIN
D8 |  | input |  | edge right | R | blue | EDGE_R_PIN
D9 |  | input | 1 | contact left | L | black | BUMPER_L_PIN
D10 |  | input | 1 | contact middle | M | black | BUMPER_M_PIN
D11 |  | input | 1 | contact right | R | black | BUMPER_R_PIN
D12 |  | input |  | signal button | SB |  | SIGNAL_BUTTON_PIN | light blue with red stripe
D13 |  | output |  | status LED | SL |  | STATUS_LED_PIN | red | Note, has built-in LED, so can't reliably be used as an input.
A0 |  | output |  | power off | PO |  | POWER_OFF_PIN | purple
A1 |  | input |  | battery voltage | BV |  | BATTERY_VOLTAGE_PIN | white
A2 |  | input |  | external power sense 2 | EP2 |  | EXTERNAL_POWER_SENSE_2_PIN | yellow
A3 |  | input |  | external power sense 1 | EP1 |  | EXTERNAL_POWER_SENSE_1_PIN | green
A4 |  | NA |  | I2C
A5 |  | NA |  | I2C
torso

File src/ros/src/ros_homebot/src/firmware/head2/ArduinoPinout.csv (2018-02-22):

Arduino Pin | Supports ADC | Supports PWM | Supports Interrupt | Mode | Function | Label | Variable | Wire Color | Notes
D0 |  |  |  | NA | USB
D1 |  |  |  | NA | USB
D2 |  |  | 1 | input | pan motor encoder A | PEA | PAN_MOTOR_ENCODER_A | white | SDA
D3 |  | 1 | 0 | input | pan motor encoder B | PEB | PAN_MOTOR_ENCODER_B | gray | SCL
D4 |  |  |  | output | pan motor phase | PPH | PAN_MOTOR_PHASE | blue
D5 |  | 0 |  | output | Ultrabright 1 | L1 | ULTRABRIGHT_LED_1
D6 |  | 0 | 1 | output | led blue | LB | STATUS_LED_BLUE | blue
D7 |  |  | 1 | input | pan motor reference position | PGA | PAN_MOTOR_POSITION_REF
D8 |  | 1 |  | output | pan motor enable (pwm) | PEN | PAN_MOTOR_ENABLE | white
D9 |  | 1 |  | output | tilt servo position set (pwm) | TS | TILT_SERVO_POS_SET
D10 |  | 1 |  | output | led green | LG | STATUS_LED_GREEN | brown
D11 |  | 0
D12 |  | 1 |  | output | led red | LR | STATUS_LED_RED | red
D13 |  | 1 |  | output | line laser | LP | LINE_LASER_SET | yellow
A0 | 1 |  |  | input | tilt servo position get | TG | TILT_SERVO_POS_GET
A1 | 1
A2 | 1
A3 | 1
A4 | 1 |  |  |  |  |  |  |  | On 12 way header.
A5 | 1 |  |  |  |  |  |  |  | On 12 way header.
head2 |  |  |  |  |  |  |  |  | http://www.hobbytronics.co.uk/arduino-uno-pro
 |  |  |  |  |  |  |  |  | https://store.arduino.cc/arduino-uno-rev3

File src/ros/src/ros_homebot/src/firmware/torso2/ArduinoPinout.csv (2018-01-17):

Arduino Pin | Interruptable | Supported Modes | Mode | PWM | Function | Label | Label Color | Variable | Wire Color | Notes
D0 |  | NA | NA |  | USB
D1 |  | NA | NA |  | USB
D2 | 1 | input/output | input |  | accel/gyro interrupt | AGI |  | ACCEL_GYRO_INT_PIN
D3 | 1 | input/output | input | 1 | ultrasonic left | L | red | SONIC_L_PIN
D4 |  | input/output | input |  | ultrasonic middle | M | red | SONIC_M_PIN
D5 |  | input/output | input |  | ultrasonic right | R | red | SONIC_R_PIN
D6 |  | input/output | input |  | edge left | L | blue | EDGE_L_PIN
D7 |  | input/output | input |  | edge middle | M | blue | EDGE_M_PIN
D8 |  | input/output | input | 1 | edge right | R | blue | EDGE_R_PIN
D9 |  | input/output | input | 1
D10 |  | input/output | input | 1
D11 |  | input/output | output |  | power off | PO |  | POWER_OFF_PIN | purple
D12 |  | input/output | input | 1 | signal button | SB |  | SIGNAL_BUTTON_PIN | light blue with red stripe
D13 |  | input/output | output | 1 | status LED | SL |  | STATUS_LED_PIN | red | Note, has built-in LED, so can't reliably be used as an input.
A0 |  | input
A1 |  | input | input |  | battery voltage | BV |  | BATTERY_VOLTAGE_PIN | white
A2 |  | input | input |  | external power sense 2 | EP2 |  | EXTERNAL_POWER_SENSE_2_PIN | yellow
A3 |  | input | input |  | external power sense 1 | EP1 |  | EXTERNAL_POWER_SENSE_1_PIN | green
A4 |  | NA | NA |  | I2C
A5 |  | NA | NA |  | I2C

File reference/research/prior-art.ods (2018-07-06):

Score | Name | Company | Assembled price | Kit price | Additional kit costs | Open software | ROS support | Open hardware | Auto-charging | Pan-tilt camera | Depth Vision | Power req. (W) | Touchscreen | WIFI | Bluetooth | Arm actuator | Omni drive | Assembled weight (kg) | URL | URL2
13.82 | Homebot |  |  | $700.00 | $0.00 | 1 | 1 | 1 | 1 | 1 | 1 | 42 | 0 | 1 | 1 | 0 | 0 | 3
9.83 | Oculus | Xaxxon | $415 | $415 | $500 | 0.5 | 0 | 0.5 | 1 | 0.5 | 1 | 2.5 | 0.5 | 0.5 | 0.5 | 0 | 0 |  | http://www.xaxxon.com/oculus
9.50 | Mockbot |  |  | $700.00 |  | 1 | 1 | 1 | 0 | 0 | 1 | 50 | 0 | 1 | 0 | 0 | 0 | 5 | https://github.com/mockbot/MockBot
9.28 | Turtle Rover | Turtle | $2,199 | $1,049.00 | $200.00 | 1 | 0 | 1 | 0 | 0 | 0 | 12 | 0 | 1 | 0 | 1 | 0 | 5 | https://turtlerover.com | https://github.com/turtleRover
9.25 | Buddy |  | $750 |  | $150.00 | 0 | 0 | 0 | 1 | 1 | 0 | 50 | 1 | 1 | 1 | 0 | 0 | 5 | https://www.indiegogo.com/projects/buddy-your-family-s-companion-robot
8.54 | Linorobot |  |  | $700.00 |  | 1 | 1 | 1 | 0 | 0 | 0 | 24 | 0 | 1 | 0 | 0 | 0 |  | https://linorobot.org
8.26 | Oculus Prime | Xaxxon | $548 | $548 | $500 | 0.5 | 0 | 0.5 | 1 | 0 | 1 |  | 0.5 | 0.5 | 0.5 | 0 | 0 |  | http://www.xaxxon.com/
8.00 | Create 2 | iRobot | $200 | $200.00 | $0.00 | 0 | 0 | 0 | 1 | 0 | 0 |  | 0 | 0 | 0 | 0 | 0 |  | http://www.irobot.com/About-iRobot/STEM/Create-2.aspx
6.50 | Builder Robot | Lunds University |  | $1,500.00 |  | 1 | 0 | 1 | 0 | 0.5 | 0 | 100 | 0 | 1 | 1 | 1 | 1 | 5 | http://www.instructables.com/id/Building-the-Builder-Robot/
5.25 | Turtlebot 2 | Clearpath Robotics | $2,000 | $2,000 | $50.00 | 1 | 1 | 0 | 1 | 0 | 1 |  | 0.5 | 0.5 | 0.5 | 0 | 0 |  | http://store.clearpathrobotics.com/products/turtlebot-2
5.00 | Zenbo | Asus | $600 | $600.00 | $0.00 | 0 | 0 | 0 | 0 | 0 | 0 |  | 1 | 1 | 0 | 0 | 0 |  | http://zenbo.asus.com/
-3.00 | Q.bo | Thecorpora | $4,000 | $3,000.00 | $0.00 | 1 | 1 | 0.5 | 0 | 1 | 1 | 100 | 0 | 1 | 0 | 0 | 0 |  |  | http://thecorpora.com/index.php/faq

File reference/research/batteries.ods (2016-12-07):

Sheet: Batteries
LiPo Score | SLA Score | Name | Base Price | Price for 12V | Dollar/energy density | Voltage | mAh | Watt hours | Energy density (watt hours/kg) | Max theoretical energy density (watt hours/kg) | High availability | Type | Built-in charger? | Pass through | Onboard charger? | Peak discharge (C) | Max safe discharge (C) | Max safe discharge (A) | Charge plug | Discharge plug | Min discharge cyles | Weight (g) | Length (cm) | Width (cm) | Height (cm) | Volume (cm^3) | Manufacturer | Man. Product Brand | Man. Product ID | URL | URL2 | Notes
0.00 | 17.88 | UPG UBCD5745 SLA | $40.00 | $40.00 | $1.01 | 12 | 18000 | 216 | 39.68 | 42.00 | 1 | sealed lead acid | 0 |  | 0 | 1 | 1 | 1.00 |  |  | 500 | 5443 | 18.2 | 16.7 | 7.7 | 2340.338 |  |  |  | https://www.amazon.com/UBCD5745-Sealed-Lead-Acid-Batteries/dp/B001DL7D1O
0.00 | 15.94 | 12V 10AH Sealed Lead Acid | $17.00 | $17.00 | $0.40 | 12 | 7000 | 84 | 42.09 | 42.00 | 1 | sealed lead acid | 0 |  | 0 |  | 0.2 | 1.40 |  |  | 100 | 1995.81 | 15 | 6.48 | 9.32 | 905.904 |  |  |  | http://www.ebay.com/itm/1270-Verizon-FIOS-Relplacement-Battery-12V-7AH-SLA-Rechargeable-F1-Terminal/140959046137
0.00 | 14.56 | UPG UB1250 SLA | $15.00 | $15.00 | $0.36 | 12 | 5000 | 60 | 41.35 | 42.00 | 1 | sealed lead acid | 0 |  | 0 | 1 | 1 | 1.00 |  |  | 500 | 1451 | 10.7 | 9 | 7 | 674.1 |  |  |  | https://www.amazon.com/UB1250-Sealed-Lead-Acid-Batteries/dp/B001DL9IBC/
0.00 | 0.00 | DC 12V 15000mAh Super Rechargeable Lithium-ion Battery Pack | $29.00 | $29.00 | $0.08 | 12 | 15000 | 180 | 370.37 | 265.00 | 1 | lithium-ion |  |  | 0 | 0.16 | 0.16 | 2.40 | 5.5*2.1mm DC jack | 5.5*2.1mm DC plug | 300 | 486 | 15 | 7 | 3.7 | 388.5 |  |  | DC12150 | http://www.banggood.com/DC-12V-15000mAh-Super-Rechargeable-Protable-Lithium-ion-Battery-Pack-p-970196.html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
0.00 | 0.00 | Portable 12V Rechargeable 9800mAh Li-po Battery | $35.00 | $35.00 | $0.12 | 12 | 9800 | 117.6 | 284.06 | 265.00 | 1 | lithium-ion polymer | 1 |  | 0 | 1 | 0.2 | 1.96 | 5.5*2.1mm DC jack | 5.5*2.1mm DC plug | 500 | 414 | 9.1 | 8 | 3 | 218.4 | Shenzhen CEE Time Technology CO., LTD? |  | T-12980/DC12980 | http://www.ebay.com/itm/Portable-12V-Rechargeable-9800mAh-Li-po-Battery-for-CCTV-Camera-MP3-Cellphone-/121440154300
0.00 | 0.00 | 12V 4000mAh Lithium-ion Super Rechargeable Battery | $13.00 | $13.00 | $0.07 | 12 | 4000 | 48 | 175.18 | 265.00 | 1 | lithium-ion | 1 |  | 0 | 1 | 0.2 | 0.80 | 5.5*2.1mm DC jack | 5.5*2.1mm DC plug | 500 | 274 | 12.9 | 6.7 | 2.4 | 207.432 |  |  | DC12400 | http://www.ebay.com/itm/12V-4000mAh-Lithium-ion-Super-Rechargeable-Battery-Pack-AC-Charger-SPC-2369-US/370921997007
0.00 | 0.00 | 12V 6800mah Li-ion Battery | $17.00 | $17.00 | $0.16 | 12 | 2266.6666666667 | 27.2 | 108.80 | 265.00 | 1 | lithium-ion | 1 |  | 0 | 1 | 0.2 | 0.45 | 5.5*2.1mm DC jack | 5.5*2.1mm DC plug | 500 | 250 | 11.5 | 6.2 | 2.1 | 149.73 |  |  | DC12680 | http://www.amazon.com/6800mAh-Capacity-Rechargeable-Lithium-Battery/dp/B00LKJGW20
0.00 | 0.00 | 12v 6800mAH Lithium-Ion Battery Pack | $30.00 | $30.00 | $0.18 | 12 | 2266.6666666667 | 27.2 | 167.90 | 265.00 | 1 | lithium-ion polymer | 1 |  | 0 |  | 0.2 | 0.45 |  |  | 300 | 162 | 11.5 | 6.2 | 2.1 | 149.73 |  |  |  | http://www.securityandselfdefensestore.com/index.php?option=com_virtuemart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
0.00 | 0.00 | 12V Rechargeable 3000mAh Li-ion Battery Pack | $14.00 | $14.00 | $0.12 | 12 | 1500 | 18 | 115.38 | 265.00 | 1 | lithium-ion polymer | 1 | 1 | 1 | 0.5 | 0.5 | 0.50 | 5.5*2.1mm DC jack | 5.5*2.1mm DC plug | 500 | 156 | 9 | 4.5 | 1.8 | 72.9 |  |  | DC12300 | http://www.amazon.com/gp/product/B00WVW086Q?psc=1&redirect=true&ref_=od_aui_detailpages00
0.00 | 0.00 | ZIPPY 5200mAh 2S2P 30C | $21.00 | $34.05 | $0.28 | 7.4 | 5200 | 38.48 | 122.55 | 265.00 | 1 | lithium-ion polymer | 0 |  | 0 | 40 | 30 |  | JST-XH | HXT4mm | 300 | 314 | 13.7 | 4.6 | 2.5 | 157.55 |  |  |  | http://www.hobbyking.com/hobbyking/store/__21000__ZIPPY_5200mAh_2S2P_30C_hardcase_pack_ROAR_APPROVED_.html
15.76 | 0.00 | ZIPPY Flightmax 2500mAh | $16.00 | $17.30 | $0.10 | 11.1 | 2500 | 27.75 | 177.88 | 265.00 | 1 | lithium-ion polymer | 0 |  | 0 | 5 | 3 | 5.00 | JST-XH |  | 300 | 156 | 9.9 | 3.1 | 2.6 | 95.139 |  |  |  | https://hobbyking.com/hobbyking/store/__6955__ZIPPY_Flightmax_2500mAh_Transmitter_Pack_Futaba_JR_.html
0.00 | 0.00 | Turnigy 3600mAh 2S 12C Lipo Receiver Pack | $20.00 | $32.43 | $0.20 | 7.4 | 3600 | 26.64 | 161.45 | 265.00 | 1 | lithium-ion polymer | 0 |  | 0 | 12 | 1 | 12.00 | JST-XH | JR style | 300 | 165 | 6.5 | 5 | 2.8 | 91 |  |  |  | http://www.hobbyking.com/hobbyking/store/__28006__Turnigy_3600mAh_2S_12C_Lipo_Receiver_Pack.html
14.48 | 0.00 | Turnigy 2200mAh 3S 20C Lipo | $10.00 | $10.81 | $0.08 | 11.1 | 2200 | 24.42 | 129.89 | 265.00 | 1 | lithium-ion polymer | 0 |  | 0 | 30 | 1 | 20.00 | JST-XH | XT60 | 300 | 188 | 10.3 | 3.3 | 2.4 | 81.576 |  |  |  | https://hobbyking.com/en_us/turnigy-2200mah-3s-20c-lipo-pack.html
0.00 | 0.00 | Turnigy 2200mAh 3S 25C Lipo Pack | $11.00 | $11.89 | $0.09 | 11.1 | 2200 | 24.42 | 129.89 | 265.00 | 1 | lithium-ion polymer | 0 |  | 0 |  | 25 | 55.00 | JST-XH | XT60 | 300 | 188 | 10.5 | 3.3 | 2.4 | 83.16 |  |  |  | http://www.hobbyking.com/hobbyking/store/__8934__Turnigy_2200mAh_3S_25C_Lipo_Pack.html
0.00 | 0.00 | ZIPPY Flightmax 2200mAh 3S1P 40C | $14.00 | $15.14 | $0.13 | 11.1 | 2200 | 24.42 | 117.97 | 265.00 | 1 | lithium-ion polymer | 0 |  | 0 | 50 | 1 | 40.00 | JST-XH | XT60 | 300 | 207 | 10.5 | 3.5 | 2.6 | 95.55 |  |  |  | http://www.hobbyking.com/hobbyking/store/__9942__ZIPPY_Flightmax_2200mAh_3S1P_40C.html
13.04 | 0.00 | Turnigy nano-tech 3000mAh 2S2P | $18.00 | $29.19 | $0.19 | 7.4 | 3000 | 22.2 | 152.05 | 265.00 | 1 | lithium-ion polymer | 0 |  | 0 | 40 | 1 | 20.00 | JST-XH | JST | 300 | 146 | 8.8 | 3.4 | 2.5 | 74.8 |  |  |  | http://www.hobbyking.com/hobbyking/store/__23821__Turnigy_nano_tech_3000mAh_2S2P_20_40C_Lipo_Receiver_Pack.html
11.08 | 0.00 | Turnigy nano-tech 1500mah 3S | $16.00 | $17.30 | $0.13 | 11.1 | 1500 | 16.65 | 129.07 | 265.00 | 1 | lithium-ion polymer | 0 |  | 0 | 70 | 1 | 35.00 | JST-XH | XT60 | 300 | 129 | 8.8 | 3.4 | 2.1 | 62.832 |  |  |  | http://www.hobbyking.com/hobbyking/store/__26453__Turnigy_nano_tech_1500mah_3S_35_70C_Lipo_Pack.html
10.30 | 0.00 | Turnigy nano-tech 2000mAh 2S1P | $13.00 | $21.08 | $0.14 | 7.4 | 2000 | 14.8 | 151.02 | 265.00 | 1 | lithium-ion polymer | 0 |  | 0 | 40 | 1 | 20.00 | JST-XH | JST | 300 | 98 | 8.7 | 3.4 | 1.7 | 50.286 |  |  |  | http://www.hobbyking.com/hobbyking/store/__23820__Turnigy_nano_tech_2000mAh_2S1P_20_40C_Lipo_Receiver_Pack.html
0.00 | 0.00 | Turnigy 1800mAh 2S 12C Lipo | $10.00 | $16.22 | $0.11 | 7.4 | 1800 | 13.32 | 144.78 | 265.00 | 1 | lithium-ion polymer | 0 |  | 0 | 12 | 1 | 12.00 | JST-XH | JR style | 300 | 92 | 6.4 | 5 | 1.4 | 44.8 |  |  |  | http://www.hobbyking.com/hobbyking/store/__28005__Turnigy_1800mAh_2S_12C_Lipo_Receiver_Pack.html
9.63 | 0.00 | Turnigy 1700mAh 2S 20C Lipo | $8.00 | $12.97 | $0.09 | 7.4 | 1700 | 12.58 | 136.74 | 265.00 | 1 | lithium-ion polymer | 0 |  | 0 | 30 | 20 | 34.00 | JST-XH | XT60 | 300 | 92 | 9.1 | 2.65 | 1.8 | 43.407 |  |  |  | http://www.hobbyking.com/hobbyking/store/__15088__Turnigy_1700mAh_2S_20C_Lipo_Pack_Suits_1_16th_Monster_Beatle_SCT_Buggy_.html
9.23 | 0.00 | ZIPPY Compact 1000mAh 3S 25C Lipo | $5.50 | $5.95 | $0.05 | 11.1 | 1000 | 11.1 | 121.98 | 265.00 | 1 | lithium-ion polymer | 0 |  | 0 | 35 | 1 | 25.00 | JST-XH | XT60 | 91 | 91 | 7.4 | 3.4 | 2 | 50.32 |  |  |  | http://www.hobbyking.com/hobbyking/store/__21334__ZIPPY_Compact_1000mAh_3S_25C_Lipo_Pack.html
8.95 | 0.00 | Turnigy 1500mAh 2S 25C Lipoly | $9.00 | $14.59 | $0.11 | 7.4 | 1500 | 11.1 | 132.14 | 265.00 | 1 | lithium-ion polymer | 0 |  | 0 | 35 | 25 | 37.50 | JST-XH | JST | 300 | 84 | 7.1 | 3.3 | 1.9 | 44.517 |  |  |  | http://www.hobbyking.com/hobbyking/store/__26564__Turnigy_1500mAh_2S_25C_Lipoly_Battery.html
0.00 | 0.00 | Turnigy nano-tech 1500mah 2S 35~70C Lipo | $10.00 | $16.22 | $0.13 | 7.4 | 1500 | 11.1 | 121.98 | 265.00 | 1 | lithium-ion polymer | 0 |  | 0 | 70 | 35 | 52.50 | JST-XH | XT60 | 300 | 91 | 8.5 | 3.5 | 1.4 | 41.65 |  |  |  | http://www.hobbyking.com/hobbyking/store/__26452__Turnigy_nano_tech_1500mah_2S_35_70C_Lipo_Pack.html
8.39 | 0.00 | Turnigy 1300mAh 2S 20C Lipo | $8.00 | $12.97 | $0.10 | 7.4 | 1300 | 9.62 | 126.58 | 265.00 | 1 | lithium-ion polymer | 0 |  | 0 | 30 | 20 | 26.00 | JST-XH | XT60 | 300 | 76 | 9 | 3 | 1.4 | 37.8 |  |  |  | http://www.hobbyking.com/hobbyking/store/__15087__Turnigy_1300mAh_2S_20C_Lipo_Pack_Suit_1_18th_Truck_.html
0.00 | 0.00 | XTPower 10000mAh External Battery Pack | $50.00 | $50.00 | $0.19 | 12 | 6200 | 74.4 | 256.55 | 265.00 | 0.5 | lithium-ion polymer | 1 |  | 0 |  |  | 0.00 |  |  | 500 | 290 |  |  |  |  | XTPower |  |  | http://www.amazon.com/XTPower-10000mAh-Recorders-Sensation-Connectors/dp/B00935L44E
0.00 | 0.00 | Lithium Ion Cylindrical Battery | $10.00 | $32.43 | $0.18 | 3.7 | 2200 | 8.14 | 176.96 | 265.00 | 1 | lithium-ion | 0 |  | 0 | 2 | 0.5 | 1.10 | JST-XH | JST-XH | 300 | 46 | 6.9 | 1.8 | 1.8 | 22.356 |  |  |  | http://www.adafruit.com/products/1781
0.00 | 0.00 | Lithium Ion Battery Pack - 3.7V 4400mAh | $20.00 | $64.86 | $0.38 | 3.7 | 4400 | 16.28 | 171.37 | 265.00 | 1 | lithium-ion | 0 |  | 0 | 2 | 0.90909091 | 4.00 |  |  | 300 | 95 | 6.9 | 3.7 | 1.8 | 45.954 |  |  |  | http://www.adafruit.com/products/354
0.00 | 0.00 | Lithium Ion Battery Pack - 3.7V 6600mAh | $30.00 | $97.30 | $0.62 | 3.7 | 6600 | 24.42 | 157.55 | 265.00 | 1 | lithium-ion | 0 |  | 0 | 2 | 0.2 | 1.32 |  |  | 300 | 155 | 6.9 | 5.4 | 1.8 | 67.068 |  |  |  | http://www.adafruit.com/product/353
0.00 | 0.00 | Polymer Lithium Ion Battery 2000mAh | $13.00 | $42.16 | $0.21 | 3.7 | 2000 | 7.4 | 205.56 | 265.00 | 1 | lithium-ion polymer | 0 |  | 0 |  | 2 | 4.00 |  |  | 300 | 36 | 6 | 5.4 | 0.58 | 18.792 |  |  |  | https://www.sparkfun.com/products/8483
0.00 | 0.00 | Tenergy Premium AA 2500mAh NiMH | $3.50 | $32.31 | $0.62 | 1.3 | 2500 | 3.25 | 104.84 | 100.00 | 1 | NiMH | 0 |  | 0 |  | 0.2 | 0.50 |  |  | 50 | 31 | 5.5 | 1.45 | 1.45 | 11.56375 |  |  |  | http://www.all-battery.com/aa2500mahhighcapacitynimhrechargeablebattery10320.aspx
0.00 | 0.00 | 12V Portable 15000mAh Li-ion Super Rechargeable Battery Pack | $70.00 | $70.00 | $0.26 | 12 | 15000 | 180 | 268.66 | 265.00 | 1 | lithium-ion | 1 |  | 0 | 0.5 | 0.2 | 3.00 | 5.5*2.1mm DC jack | 5.5*2.1mm DC plug | 500 | 670 | 13 | 6.6 | 4.5 | 386.1 | Shenzhen CEE Time Technology CO., LTD? | Zandee | DC121500 | http://www.ebay.com/itm/12V-Portable-15000mAh-Li-ion-Super-Rechargeable-Battery-Pack-Portable-for-CCTV-/221661421623
0.00 | 0.00 | Patriot FUEL+ 9000mA | $30.00 | $72.00 | $0.29 | 5 | 9000 | 45 | 247.25 | 265.00 | 0.25 | lithium-ion | 1 | 1 | 1 | 0.5 |  | 0.00 | USB | USB | 500 | 182 | 9.4 | 6.3 | 2.5 | 148.05 |  |  |  | http://www.amazon.com/gp/product/B00DWPMU12?psc=1&redirect=true&ref_=oh_aui_detailpage_o02_s00 |  | Unreliable UPS.
0.00 | 0.00 | Anker® 2nd Gen Astro E3 | $23.00 | $55.20 | $0.26 | 5 | 10000 | 50 | 215.52 | 265.00 | 1 | lithium-ion polymer | 1 |  | 1 | 0.2 | 0.2 | 2.00 | USB | USB | 500 | 232 | 13 | 6.6 | 1.5 | 128.7 |  |  |  | http://www.amazon.com/10000mAh-Portable-External-Technology-Motorola/dp/B009USAJCC
0.00 | 0.00 | RAVPower 2nd Gen | $50.00 | $120.00 | $0.50 | 5 | 14000 | 70 | 242.21 | 265.00 | 1 | lithium-ion polymer | 1 |  | 1 | 0.07 | 0.07 | 0.98 | USB | USB | 500 | 289 | 12.1 | 8.1 | 2 | 196.02 |  |  |  | http://www.amazon.com/dp/B00EHEEFWY/?tag=hotoge-20
0.00 | 0.00 | Jackery Giant+ 2-USB Portable External Battery | $40.00 | $96.00 | $0.47 | 5 | 12000 | 60 | 204.08 | 265.00 | 1 | lithium-ion polymer | 1 |  | 1 | 0.07 | 0.07 | 0.84 | USB | USB | 500 | 294 | 10.9 | 7.8 | 2 | 170.04 |  |  |  | http://www.amazon.com/dp/B00AB174ZW/?tag=hotoge-20
0.00 | 0.00 | USB Battery Pack for Raspberry Pi | $50.00 | $120.00 | $0.72 | 5 | 10000 | 50 | 166.67 | 265.00 | 1 | lithium-ion polymer | 1 |  | 1 | 0.2 | 0.2 | 2.00 | USB | USB | 500 | 300 | 7.2 | 2.4 | 12.5 | 216 |  |  |  | https://www.adafruit.com/products/1566
0.00 | 0.00 | DC12V 12000mAh Super Rechargeable Portable Li-ion Battery | $59.00 | $59.00 | $0.23 | 12 | 12000 | 144 | 252.63 | 265.00 | 1 | lithium-ion | 1 |  | 0 |  | 0.2 | 2.40 |  |  | 500 | 570 | 11.4 | 6.8 | 4.4 | 341.088 | Shenzhen CEE Time Technology CO., LTD? | Fonly | DC1212A | http://www.ebay.com/itm/DC12V-12000mAh-Super-Rechargeable-Portable-Li-ion-Battery-US-Plug-for-CCTV-NEW/171715438036 | http://www.alibaba.com/product-detail/Super-polymer-lithium-ion-battery-12v_60180425649.html
0.00 | 0.00 | 12V 6800mAh Li-ion Rechargeable Battery | $50.00 | $50.00 | $0.30 | 12 | 2266.6666666667 | 27.2 | 167.90 | 265.00 | 1 | lithium-ion | 1 |  | 0 |  | 0.2 | 0.45 |  |  | 500 | 162 | 11.5 | 5.8 | 2 | 133.4 |  |  |  | http://www.ebay.ie/itm/330746244514?ssPageName=STRK:MEWNX:IT&_trksid=p3984.m1439.l2649
0.00 | 0.00 | Optimum Battery LiFePO4 12.8V | $140.00 | $140.00 | $1.16 | 12 | 10000 | 120 | 120.36 | 110.00 | 0 | lithium iron phosphate | 0 |  | 0 |  | 2 | 20.00 |  |  | 2000 | 997 | 16 | 6 | 9.3 | 892.8 |  |  |  | http://thecorpora.com/index.php/optimumbattery | http://www.amazon.com/Tenergy-LiFePO4-Lithium-Phosphate-Battery/dp/B0056BEJCI?s=aps
0.00 | 0.00 | Tenergy 12 Volt 10Ah LiFePO4 Battery | $160.00 | $160.00 | $1.61 | 12 | 10000 | 120 | 99.09 | 110.00 | 1 | lithium iron phosphate | 0 |  | 0 |  | 2.5 | 25.00 |  |  | 300 | 1211 | 15 | 6 | 9.5 | 855 |  |  |  | http://www.tenergy.com/31383
0.00 | 0.00 | Energizer AA lithium | $3.00 | $24.00 | $7.73 | 1.5 | 3000 | 4.5 | 310.34 | 265.00 | 1 | lithium | 0 |  | 0 |  |  | 0.00 |  |  | 1 | 14.5 | 5.05 | 1.45 | 1.45 | 10.617625 |  |  |  | http://www.alliedelec.com/energizer-l91bp-4/70145453/
0.00 | 0.00 | Duracell AA alkaline | $1.90 | $15.20 | $11.10 | 1.5 | 2100 | 3.15 | 136.96 | 200.00 | 1 | alkaline | 0 |  | 0 |  | 0.5 | 1.05 |  |  | 1 | 23 | 5 | 1.5 | 1.5 | 11.25 |  |  |  | http://www.alliedelec.com/duracell-mn1500bkd/70149224/
0.00 | 0.00 | Turnigy nano-tech Ultimate 6400mah 2S2P | $61.00 | $98.92 | $0.68 | 7.4 | 6400 | 47.36 | 145.28 | 265.00 | 1 | lithium-ion polymer | 0 |  | 0 | 90 | 1 | 90.00 | JST-XH | 5mm Bullet-Connector | 300 | 326 | 9.3 | 6.8 | 2.5 | 158.1 |  |  |  | http://www.hobbyking.com/hobbyking/store/__51842__Turnigy_nano_tech_Ultimate_6400mah_2S2P_90C_Hardcase_Lipo_Square_Pack.html
0.00 | 0.00 | ZIPPY Flightmax 6200mah 1S 30C | $18.00 | $58.38 | $0.46 | 3.7 | 6200 | 22.94 | 128.16 | 265.00 | 1 | lithium-ion polymer | 0 |  | 0 | 30 | 1 | 30.00 | HXT |  | 300 | 179 | 9.2 | 4.6 | 1.9 | 80.408 |  |  |  | http://www.hobbyking.com/hobbyking/store/__19635__ZIPPY_Flightmax_6200mah_1S_30C_Hardcase_Car_Lipoly.html

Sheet: Constraints
Name | Value
Max Width (cm) | 3.4
Max Height (cm) | 2.8
Max Length (cm) | 10.3
SLA Max Width (cm) | 20
SLA Max Height (cm) | 20
SLA Max Length (cm) | 20

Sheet: Reference
http://en.wikipedia.org/wiki/Lithium-ion_battery
http://en.wikipedia.org/wiki/Lithium_iron_phosphate_battery

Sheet: Measurements
Score | Name | average load (A) | v0 | v1 | t0 | t1 | td (minutes) | td (hours) | m | b | total discharge hours | regulator | Notes
0.20 | 12V Rechargeable 1500mAh 3S Li-ion Battery Pack | 0.6 | 11.84 | 10.84 | 05/05/16 07:14 PM | 05/05/16 08:26 PM | 72 | 1.20 | -0.01 | 11.84 | 2.84 | dc-dc
0.27 | Turnigy 1700mAh 2S 20C Lipo (1) | 0.6 | 7.56 | 3.86 |  |  | 97 | 1.62 | -0.04 | 7.56 | 0.66 | dc-dc
0.27 | Turnigy 1700mAh 2S 20C Lipo (2) | 0.6 | 7.67 | 3.85 |  |  | 96 | 1.60 | -0.04 | 7.67 | 0.64 | dc-dc
0.14 | Zippy 4000mAh 2S | 0.6 | 7.4 | 7.14 | 05/06/16 02:54 PM | 05/06/16 03:43 PM | 49 | 0.82 | -0.01 | 7.40 | 4.65 | dc-dc | robomagellan
0.00 | 12V Rechargeable 3000mAh 3S Li-ion Battery Pack | 0.6 |  |  |  |  | 0 | 0.00 | #DIV/0! | #DIV/0! | #DIV/0! | kingkong ubec
0.50 | Turnigy 1700mAh 2S 20C Lipo (1) | 0.6 | 8.28 | 5.2 | 05/06/16 09:38 PM | 05/07/16 12:39 AM | 181 | 3.02 | -0.02 | 8.28 | 1.62 | kingkong ubec
0.53 | Turnigy 1700mAh 2S 20C Lipo (2) | 0.6 | 8.35 | 6.68 | 05/07/16 12:48 AM | 05/07/16 04:00 AM | 192 | 3.20 | -0.01 | 8.35 | 3.20 | kingkong ubec
0.00 | Zippy 4000mAh 2S | 0.6 |  |  |  |  | 0 | 0.00 | #DIV/0! | #DIV/0! | #DIV/0! | kingkong ubec
0.47 | Turnigy 3000mAh 2S | 0.6 | 7.43 | 6.4 | 05/13/16 07:24 PM | 05/13/16 10:12 PM | 168 | 2.80 | -0.01 | 7.43 | 4.04 | kingkong ubec
1.00 | Turnigy 3000mAh 2S | 0.6 | 8.14 | 7.09 | 05/13/16 10:42 PM | 05/14/16 04:43 AM | 361 | 6.02 | 0.00 | 8.14 | 9.33 | kingkong ubec
0.65 | 1-cell 3000mAh | 0.6 | 3.89 | 3.35 | 05/14/16 02:41 PM | 05/14/16 06:35 PM | 234 | 3.90 | 0.00 | 3.89 | 5.62 | powerboost
0.00 | Turnigy 2200mAh 3S 20C Lipo | 0.6

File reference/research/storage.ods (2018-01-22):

Score | Name | Price | Capacity (GB) | Interface | Interface Version | Depth (mm) | Width (mm) | Height (mm) | URL
0.00 | MyDigitalSSD 128GB OTG | $60 | 128 | USB | 3 | 87.122 | 48.006 | 9.906 | https://www.amazon.com/dp/B00EZ2FRU2
0.00 | Shadow Mini | $89 | 128 | USB | 3 | 101.6 | 58.42 | 10.16 | https://www.amazon.com/Shadow-trade-External-256GB-Portable/dp/B00J5UUBNW
12.08 | PNY Elite 240GB USB 3.0 | $100 | 240 | USB | 3 | 60 | 35 | 9 | https://www.amazon.com/dp/B01GQPXBQC/

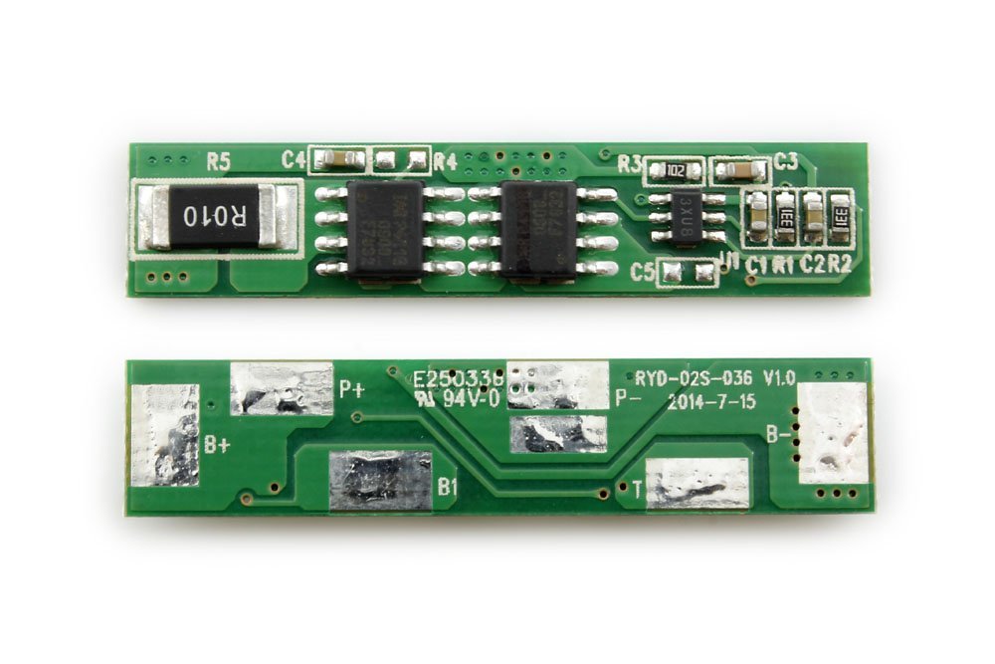
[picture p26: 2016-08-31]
reference/parts/2S Lipo Protection Board/61La20EPhGL._SL1000_.jpg

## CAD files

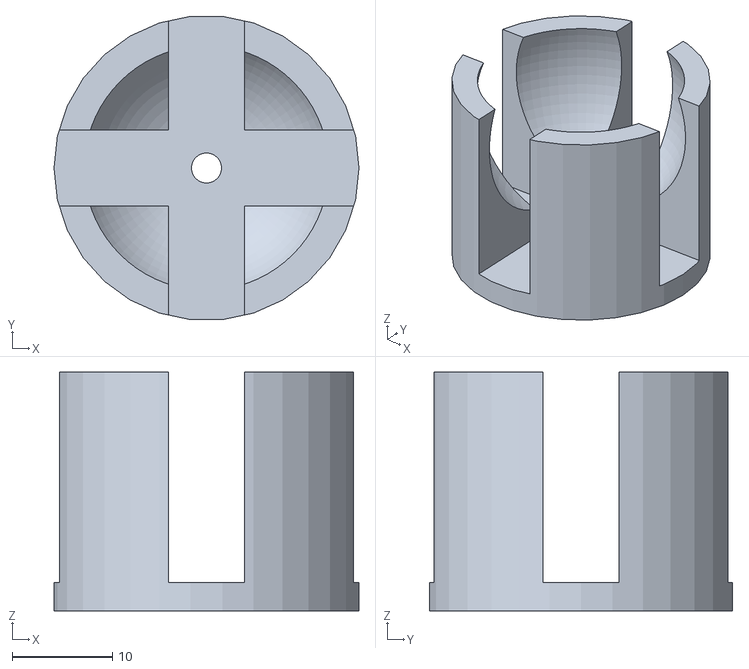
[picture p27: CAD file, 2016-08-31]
models/casters/ball_caster_v2_20150622.stl
30.4 x 30.3 x 23.8

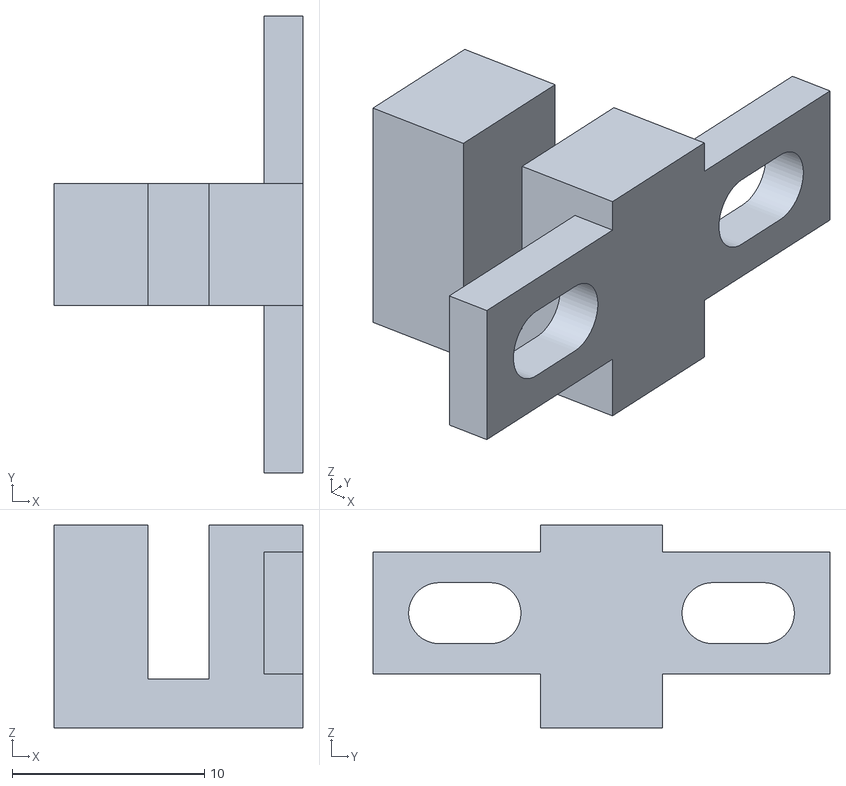
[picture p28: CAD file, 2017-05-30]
models/electronics/photointerrupter_OPB940.stl
12.9 x 23.8 x 10.5

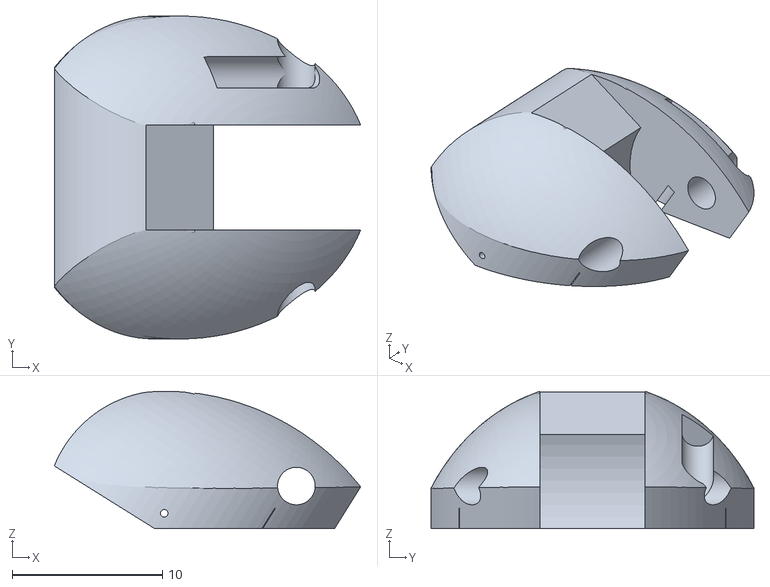
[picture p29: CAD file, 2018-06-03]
models/printable/caster_housing_center_top.stl
20.4 x 21.5 x 9.14

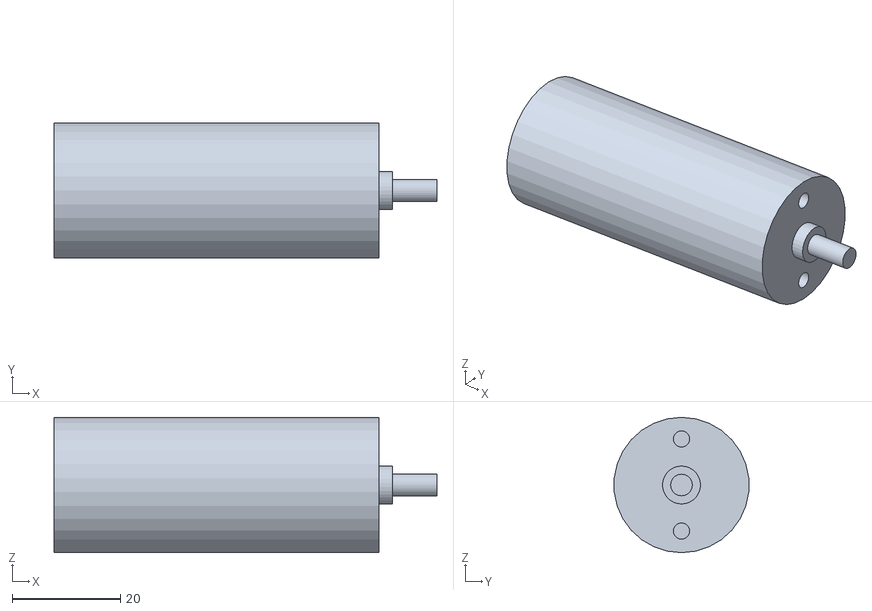
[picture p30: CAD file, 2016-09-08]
models/electronics/pololu_drive_motor.stl
70.8 x 24.9 x 25.0

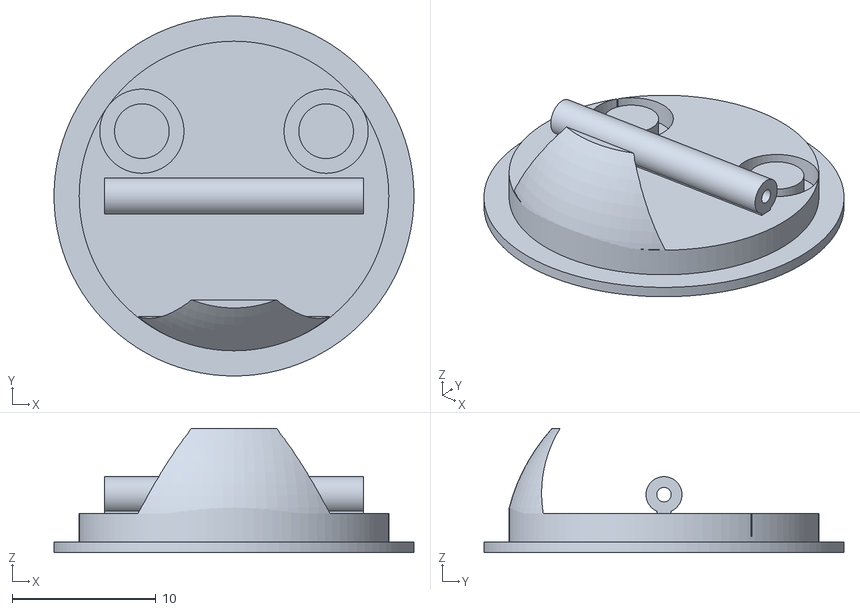
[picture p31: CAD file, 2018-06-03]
models/printable/caster_housing_center_bottom.stl
25.0 x 25.0 x 8.62

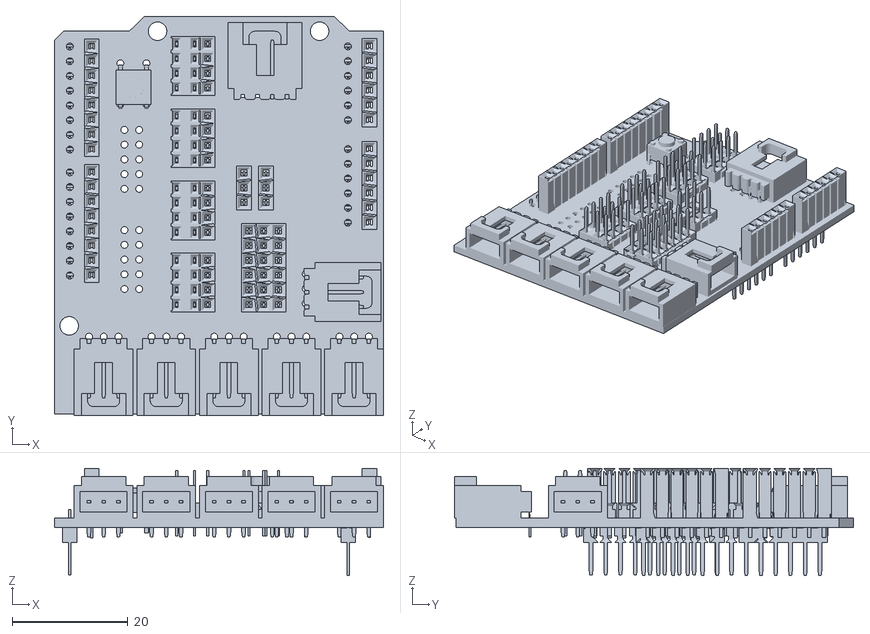
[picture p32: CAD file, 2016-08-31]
models/electronics/Arduino_Sensor_Shield.stl
56.7 x 68.8 x 18.5

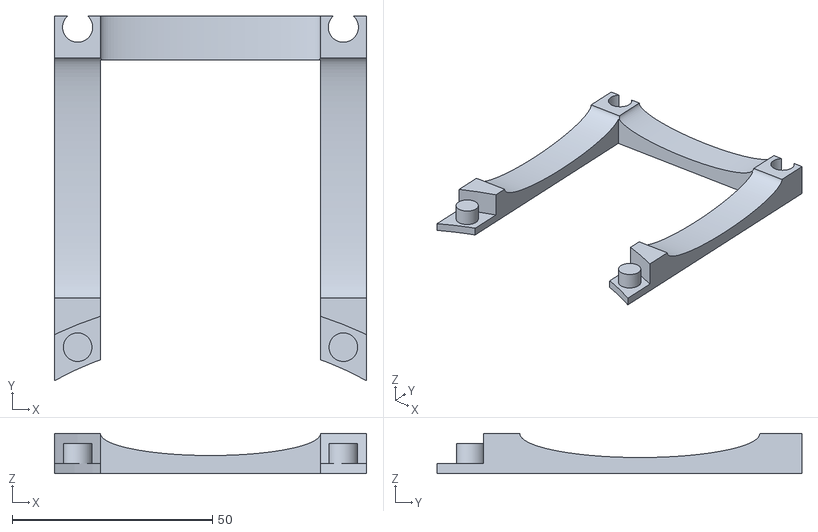
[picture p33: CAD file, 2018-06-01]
models/printable/dock_mast_recessor.stl
78.0 x 91.2 x 10.0

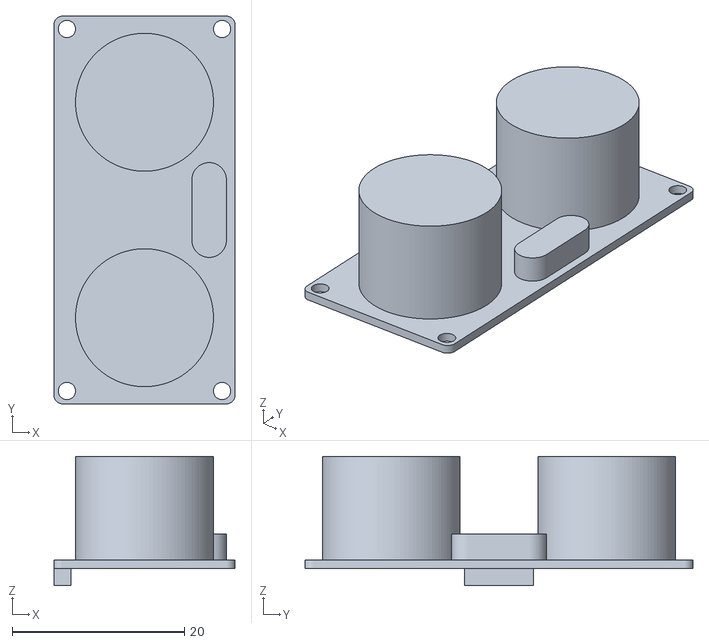
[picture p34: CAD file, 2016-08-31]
models/electronics/SEN136B5B_Ultrasonic_Sensor.stl
21.0 x 45.0 x 15.0

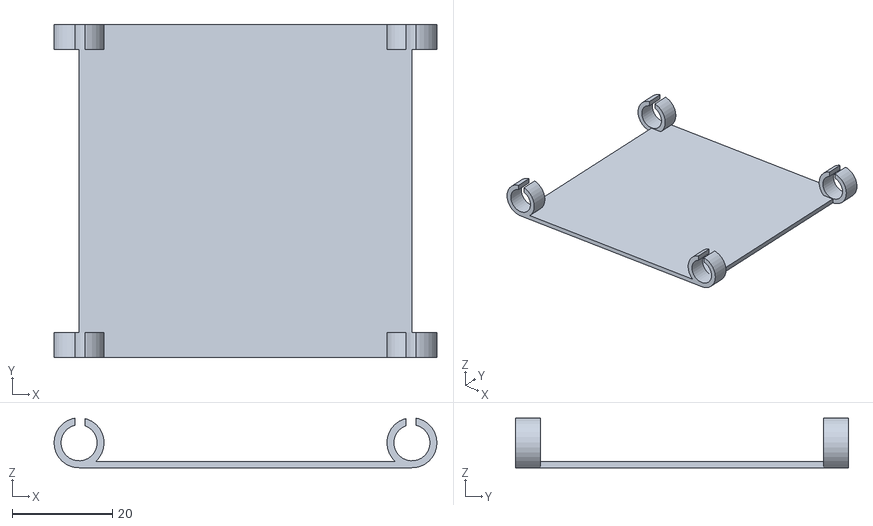
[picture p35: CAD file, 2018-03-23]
models/printable/dock_masthead.stl
76.4 x 66.5 x 9.91

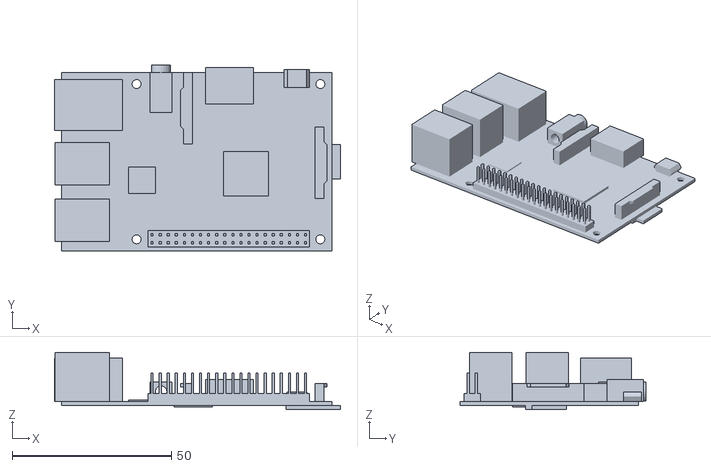
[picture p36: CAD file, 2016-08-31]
models/electronics/RPi2_01.stl
89.9 x 58.4 x 18.0

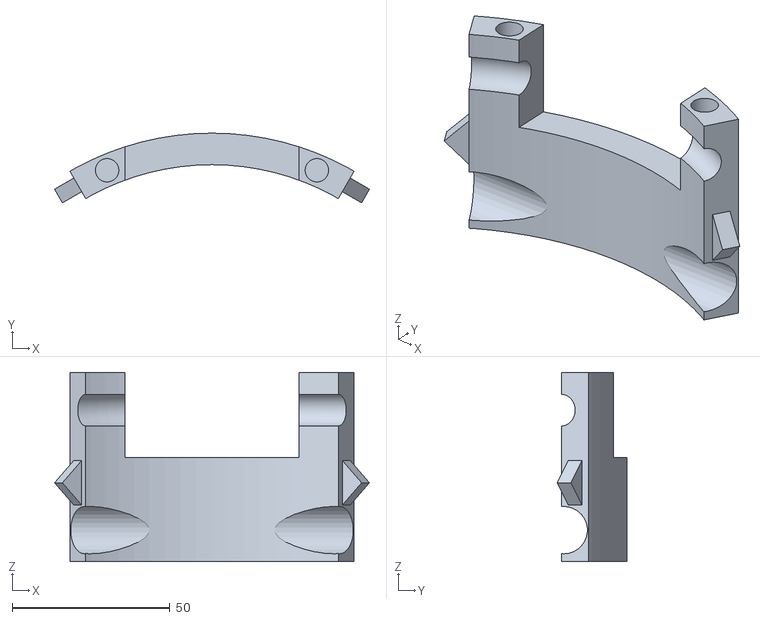
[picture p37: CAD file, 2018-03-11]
models/printable/dock_rim_part3.stl
99.7 x 22.1 x 60.0

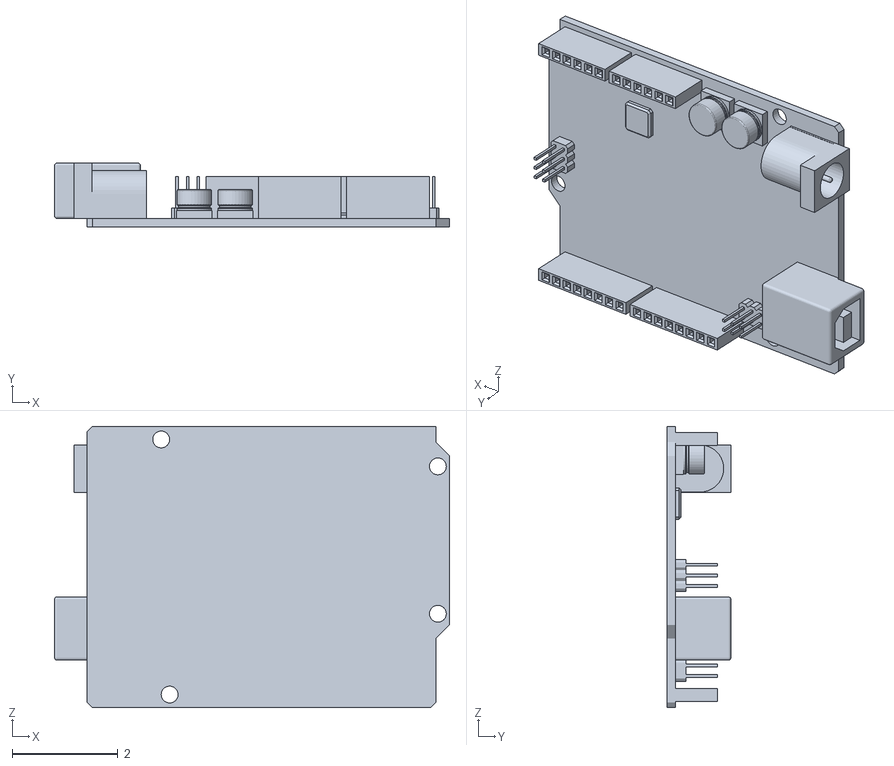
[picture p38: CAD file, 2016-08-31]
models/electronics/Arduino_UNO.stl
7.48 x 1.21 x 5.33

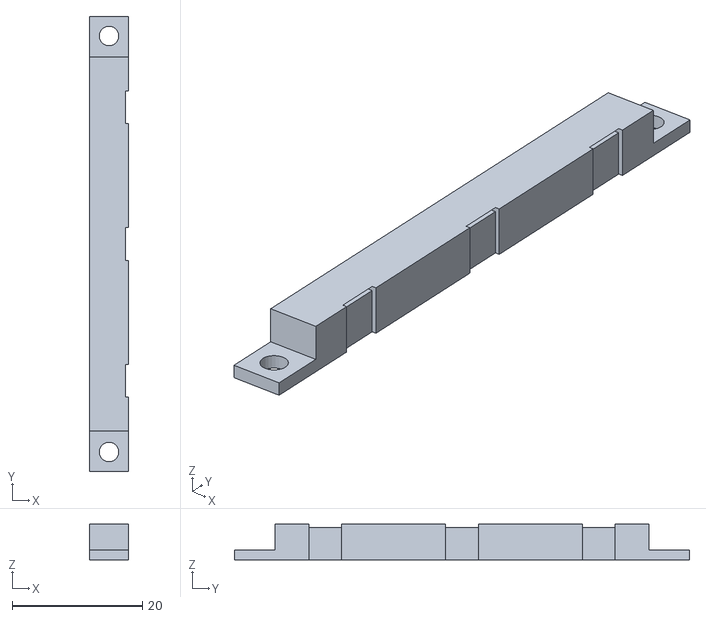
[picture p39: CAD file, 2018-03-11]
models/printable/battery_tray3_support.stl
6.00 x 70.0 x 5.50

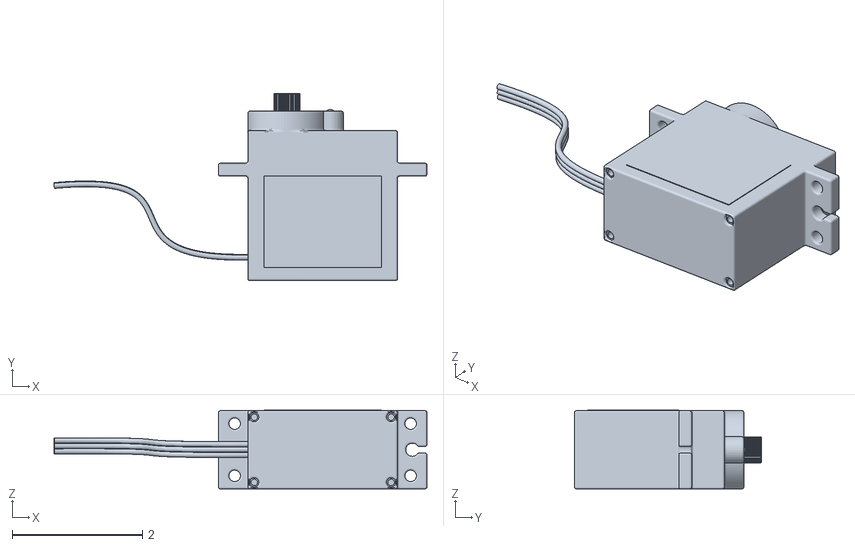
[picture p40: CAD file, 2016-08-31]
models/electronics/Servo HXT900 Micro.stl
5.72 x 2.87 x 1.21

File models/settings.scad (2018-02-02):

// Common settings used by all scad files.

// ALL UNITS IN MILLIMETERS (MM)!!!

$fn = 30;//low-res but fast to render
//$fn = 50;//higher-res but slow to render

pi = 3.1415926535897932384626433832795;

max_footprint = 150; // 15x15 cm

bottom_clearance = 10;
bottom_clearance = 25.4/2+10;
//bottom_clearance = 30;

shell_alpha = 0.215;
//shell_alpha = 1.0;

tolerance = 0.5;

// Flat countersunk M2.5mm x 0.45mm machine screw.
screw_thread_diameter = 2.5;//2.8;//2.75;//2.4?
screw_thread_length = 5;//?
screw_head_diameter = 4.75; // M2.5
//screw_head_diameter = 5.2; // M3
screw_head_height = 1.5;//2;

screw_thread_diameter2 = 2;

unit_thickness = 5;
u = unit_thickness;

shell_thickness = unit_thickness;

// Show flags.
show_platform = 1;
show_head = 1;
show_head_shell = 0;
show_head_electronics_bb = 0;
show_inner_head = 0;
show_battery = 1;
show_foot_cube = 0;
show_torso = 0;
show_motor = 0;
show_motor_wheeled_layout = 1;
show_motor_treads = 0;
show_motor_plates = 1;
show_motor_inner_plates = 1;
show_motor_outer_plates = 1;
show_wheel = 0;//obsolete
show_tracks = 1;//
show_track_wheels = 1;
show_caster = 0;
show_rpi = 1;
show_vertical_plates = 1;//
show_horizontal_plates = 1;//
show_caster_plates = 0;//obsolete?
show_camera = 1;
show_screen = 0;
show_edge_mount = 1;
show_sonar_mount = 1;
show_recharge_mount = 1;
show_conduit = 1;
show_torso_shell = 0;
show_recharge_dock = 0;
show_head_tilt_axis = 0;
show_rpi_camera_axis = 0;
show_laser_axis = 0;

head_vertical_angle_tilt = 0;
//head_vertical_angle_tilt = 30;//max
//head_vertical_angle_tilt = 10;

torso_height = 120+20;

base_plate_diameter = max_footprint-unit_thickness*2;
base_plate_frame = 0;

head_height = 50;
head_offset_z = max_footprint/2;
head_middle_cutout = 85;

rpi_with_four_hats_and_clearance = 76;

motor_gear_teeth = 26;

qrd1114_w = 6.10;
qrd1114_l = 4.39;
qrd1114_h = 4.65;

dock_radius = 10;
dock_gripper_border = 2;
dock_gripper_instep = 0.9;
dock_gripper_cutout_tapper = 50;
dock_receiver_height = 5;

// Patriod Fuel+ 9000 mAh
battery_length = 90;
battery_width = 57;
battery_height = 23;
battery_offset_z = 30;//4;

wheel_diameter = 50;
wheel_offset_x = 65;
wheel_offset_z = wheel_diameter/2;
wheel_axle_diameter = 5;

//caster_diameter = 19.05; // 0.75 inches
caster_diameter = 25.45; // 1 inches
//caster_diameter = 15.875; // 5/8 inches
caster_holder_diameter = 30;//31;
caster_offset_y = base_plate_diameter/2 - caster_holder_diameter/2;

arduino_offset_x = 0;
arduino_offset_y = 0;
arduino_offset_z = 67;
arduino_offset_x2 = 0;
arduino_offset_y2 = -20;
arduino_offset_z2 = torso_height+bottom_clearance;

horizontal_plate_width = unit_thickness*8*2 - unit_thickness*2;
horizontal_plate_depth = unit_thickness*8*2;

vertical_plate_width = horizontal_plate_depth;
vertical_plate_height = unit_thickness*8;
vertical_plate_offset_x = wheel_offset_x-22.5;
vertical_plate_offset_z = vertical_plate_height/2 + unit_thickness/2;

vertical_battery_plate_height = 100 - 15;

caster_plate_width = horizontal_plate_width + unit_thickness*2;
caster_plate_mount_length = unit_thickness*4;
caster_plate_width_minor = caster_holder_diameter;

motor_switch_length = 20;
motor_switch_thickness = 6.5;
motor_switch_height = 11;
motor_switch_height_leads = 23;
motor_switch_on_height =  13.3;
motor_switch_hole_diameter = 2.5;
motor_switch_hole_offset_z = 6.5;//this plus diameter/2 is hole center from switch top
motor_switch_hole_spacing = 7.1;// holes are diameter/2 from this

motor_length = 60;
motor_width = 25;
motor_collar_width = 7;
motor_collar_height = 2.5;
motor_axle_width = 4;
motor_axle_height = 9.5;
motor_offset_x = 10;
//motor_offset_y = motor_width/2+5;
motor_offset_y = unit_thickness*3.5;
motor_offset_z = vertical_plate_height/2 - unit_thickness/2;//4;//30;
motor_mount_holes_dist = 17;
// motor countersink hole
motor_mount_holes_width = 3; // M3
motor_mount_holes_head_height = 2.2;
motor_mount_holes_head_width = 5.8;
motor_bearing_outer_diameter = 10;
motor_bearing_inner_diameter = 5.95;
motor_bearing_thickness = 2.5;

motor_unimount_idler_axle_d = screw_thread_diameter;
//motor_unimount_spacer_depth = 0.1;//too small
motor_unimount_spacer_depth = 0.5;

motor_arm_offset_y = -u*3;
motor_arm_offset_z = u*.5;

motor_plate_width = vertical_plate_width;
motor_plate_height = vertical_plate_height;
motor_plate_thickness = unit_thickness;
motor_plate_offset_z = vertical_plate_offset_z;

motor_plate_middle_thickness = 5;

wheel_hub_offset = u*3;

motor_hole_height_offset = -5;

nylon_spacer_outer_diameter = 6.35;
nylon_spacer_inner_diameter = 3.302;
nylon_spacer_length = 12.7;

track_width = unit_thickness*3;
track_offset_x = -50;
track_offset_z = .1;
//track_wheel_radius = 19;//original
track_wheel_radius = 14;
//track_wheel_hole_radius = (nylon_spacer_outer_diameter+1)/2;
track_wheel_hole_radius = motor_bearing_outer_diameter/2;

track_driver_hole_radius = (motor_axle_width)/2 + 0.1;
track_driver_set_screw_head_d = 4.1;
track_driver_set_screw_shaft_d = 2.4;
//track_wheel_width = 13.5;//original
track_wheel_width = u*2;
track_wheel_width_buffer = u*0.25;
track_offset = 3;        //distance from chassis
track_wheel_offset = track_offset;
//track_length = 250; // see tread_triangle.py, too big
//track_length = 240; // see tread_triangle.py
//track_length = 238; //inc/dec in 10 unit increments so notches match idlers
track_length = 228; //inc/dec in 10 unit increments so notches match idlers
track_radius = track_length/2/pi;
track_wheel_show_fancy = 1;
track_wheel_gap = track_wheel_width + track_wheel_width_buffer*2;
track_axle_bearing_diameter = motor_bearing_inner_diameter - 0.1;
track_tensioner_radius = 12;
track_nut_height = 3.5; //TODO
track_punchout_thickness = 0.25;//should be the same as the minimum layer thickness

head_slew_bearing_outer_diameter = 115;
head_slew_bearing_ring_thickness = 20;
head_slew_bearing_inner_diameter = head_slew_bearing_outer_diameter - head_slew_bearing_ring_thickness;
//head_slew_bearing_hole_diameter = head_slew_bearing_inner_diameter - head_slew_bearing_ring_thickness;
head_slew_bearing_hole_diameter = 12+tolerance; // slip ring https://www.adafruit.com/products/775
//head_slew_bearing_ball_diameter = 5;
head_slew_bearing_ball_diameter = 2.5; //u/2;
head_slew_bearing_height = u;//head_slew_bearing_ball_diameter*2;
head_slew_bearing_gap = 0.5;
head_slew_bearing_slew_gap = 0;
head_slew_bearing_gap_factor = 0.1;

neck_strut_width = u*7;
neck_strut_height = u*18;
neck_strut_spacing = u*8;

show_outer_race = 0;
show_inner_race_a = 1;
show_inner_race_b = 1;
show_balls = 0;

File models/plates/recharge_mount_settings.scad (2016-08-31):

include <../settings.scad>;

recharge_mount_width = u*8;//-u*.5; //u*26;//inner box and first unit of motor mount
recharge_mount_height = u*4;//-u*.5;
recharge_mount_thickness = 2;

recharge_mount_terminal_offset = u*2;
recharge_mount_terminal_extend = 4.5;

recharge_mount_slot_mag = 1;

// radius of rounded cube used for the indentation
recharge_plug_box_r = 2;

recharge_plug_female_box_tol_xz = 0; // subtraction of width and height
recharge_plug_female_box_tol_y = 1.5; // offset in depth

//recharge_plug_male_box_tol_xz = 2.5; // subtraction of width and height
recharge_plug_male_box_tol_xz = 4.5; // subtraction of width and height
recharge_plug_male_box_tol_y = 1.5; // offset in depth

recharge_plug_terminal_extension = 0;

recharge_plug_wire_d = 2.75;

recharge_dock_width = u*20;

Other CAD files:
models/printable/dock_rim_part4.stl
models/electronics/Hitec311_Servo.stl
models/printable/dock_retainer.stl
models/printable/battery_tray3_cartridge_bottom.stl
models/gears/parametric_involute_gear_mcad_20150830.scad
models/gears/parametric_involute_gear_v5.0.scad
models/bearings/ThrustBearing.scad
models/bearings/bearing.scad
models/bearings/bearing_gradient_dashed.scad
models/bearings/slew_bearing.scad
models/bearings/slew_bearing_generator_201508.scad
models/bearings/slew_bearing_inner_bottom.scad
models/bearings/slew_bearing_inner_top.scad
models/bearings/slew_bearing_outer.scad
models/bearings/slew_bearing_outer_mount.scad
models/bearings/slew_bearing_test.scad
models/casters/BallCaster.scad
models/casters/BallCasterV2.scad
models/casters/ball-bearing-caster.scad
models/casters/caster.scad
models/casters/chair-caster.scad
models/dock/dock.scad
models/dock/dock_mast_recessor.scad
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

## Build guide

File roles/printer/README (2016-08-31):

This role represents the computer hosting the 3D printer.

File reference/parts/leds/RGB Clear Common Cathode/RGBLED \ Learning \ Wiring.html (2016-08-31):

Wiring cover (http://wiring.org.co/) Search wiring.org.co:

Cover (http://wiring.org.co/) \ Exhibition (http://wiring.org.co/exhibition/) \ Reference (http://wiring.org.co/reference/) \ Learning (http://wiring.org.co/learning/tutorials) \ Hardware (http://wiring.org.co/hardware/) \ Download (http://wiring.org.co/download/) \ About (http://wiring.org.co/about.html) »Feed (http://feed.wiring.co/) »Forum (http://forum.wiring.co/) »Wiki (http://wiki.wiring.co/) »Code (https://github.com/WiringProject/Wiring/)

Tutorials (http://wiring.org.co/learning/tutorials//): \ Examples: Basics (http://wiring.org.co/learning/basics/), Library (http://wiring.org.co/learning/libraries/), Topics (http://wiring.org.co/learning/topics/) \ Books (http://wiring.org.co/learning/books/)

Transmissive optical sensor (http://wiring.org.co/learning/basics/opticalsensor.html) | | Motor speed (http://wiring.org.co/learning/basics/motorspeed.html)

This example is for Wiring version 1.0 build 0100+. If you have a previous version, use the examples included with your software. If you see any errors or have comments, please let us know (http://forum.wiring.co/index.php/board,13.0.html).

RGB LED by BARRAGAN http://barraganstudio.com

Demonstrates the use of PWM pins (analog output) to change the color of an RGB LED. On Wiring v1 boards the PWM capable pins are: 29, 30, 31, 35, 36 and 37 On Wiring S board the PWM capable pins are: 4, 5, 6, 7, 19 and 20

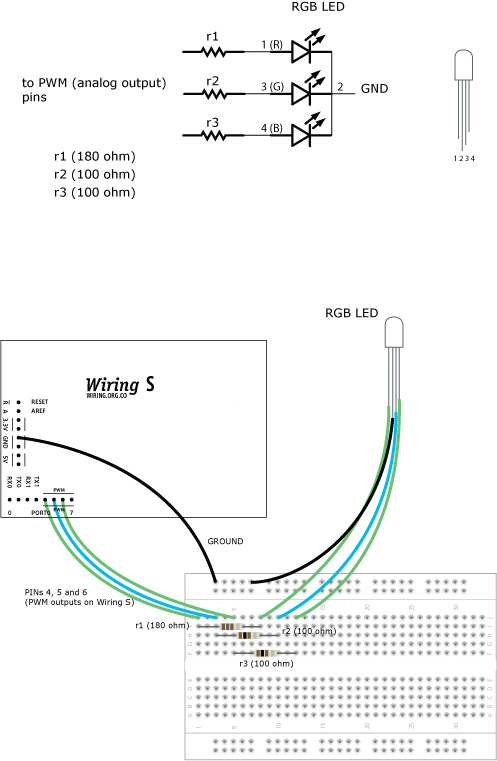
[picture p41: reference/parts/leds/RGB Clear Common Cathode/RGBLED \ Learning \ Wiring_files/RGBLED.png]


int REDPin = 4;    // RED pin of the LED to PWM pin 4
int GREENPin = 5;  // GREEN pin of the LED to PWM pin 5
int BLUEPin = 6;   // BLUE pin of the LED to PWM pin 6
int brightness = 0; // LED brightness
int increment = 5;  // brightness increment

void setup()
{
  pinMode(REDPin, OUTPUT);
  pinMode(GREENPin, OUTPUT);
  pinMode(BLUEPin, OUTPUT);
  Serial.begin(9600);
}

void loop()
{
  brightness = brightness + increment;  // increment brightness for next loop iteration

  if (brightness <= 0 || brightness >= 255)    // reverse the direction of the fading
  {
    increment = -increment;
  }
  brightness = constrain(brightness, 0, 255);
  analogWrite(REDPin, brightness);
  analogWrite(GREENPin, brightness);
  analogWrite(BLUEPin, brightness);

  delay(20);  // wait for 20 milliseconds to see the dimming effect
}

Wiring is an open project initiated by Hernando Barragán (http://barraganstudio.com/). It is developed by a small team of volunteers (http://wiring.org.co/about.html).

© Info (http://wiring.org.co/copyright.html), Processing © Info (http://processing.org/copyright.html)

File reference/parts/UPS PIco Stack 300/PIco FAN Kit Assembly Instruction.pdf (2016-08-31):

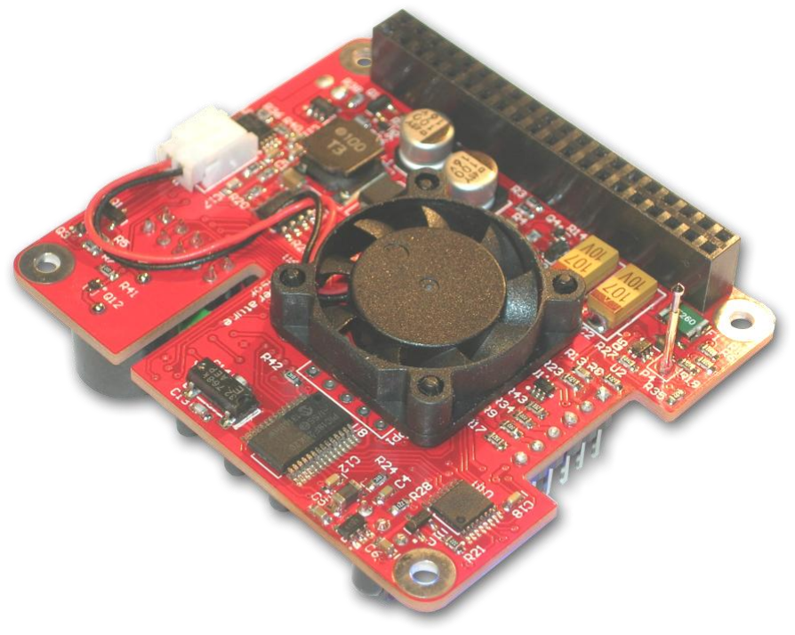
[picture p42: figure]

Designed and Manufactured by PiModules and ModMyPi
www.pimodules.com | www.modmypi.com

# PIco FAN Kit

# Pulse width modulated FAN Kit with

I

2

# C control Interface

for use with

# Raspberry Pi® B+, A+, B, and A

## works with UPS PIco installed

# HAT Compliant

“Raspberry Pi” is a trademark of the Raspberry Pi® Foundation

## © PiModules & ModMyPi

## Intelligent Modules for your Raspberry Pi®

System Overview

Introduction

The PIco FAN Kit is an Advanced Active Cooling System for the Raspberry Pi ® that can be easy installed on the UPS PIco. It is suitable for all Raspberry Pi® users whose board reaches a high temperature, for whatever reason. There is no need for any additional cabling or power supply, as the PIco FAN is directly powered and controlled via UPS PIco supervising circuits. A small hand work is needed in order to install the PIco FAN, solder an additional temperature sensor, as also the connector for the PIco FAN to the UPS PIco board. All required parts are included in the kit.

The PIco FAN Kit is equipped with an embedded temperature measurement system that continuously checks the Raspberry Pi® PCB temperature with a dedicated sensor and, according to the measured temperature, the micro controller starts, stops, or regulates the rotational speed of the embedded micro-fan.

Thanks to the Special Air Distribution Slots on the UPS PIco PCB , the PIco FAN cools not only the microprocessor on the Raspberry Pi® board but all the heat-generating devices, as well as the whole Raspberry Pi® PCB and UPS PIco.

The embedded microcontroller is easily accessible by the user through the I² C
interface and allows reading of the measured temperature, setting of temperature threshold, as well as starting/stopping/changing the speed of the embedded micro fan. The PIco FAN in ultra low noise and speed is PWM regulated with the following levels: 0 %, 25%, 50%, 75% and 100%.

Applications
The UPS Pico features an implemented Automatic Temperature Control PWM FAN controller, and can be equipped with a micro fan kit, which enables the use of the Raspberry Pi® in extreme conditions including very high temperature environments.

Features

The list of features of the UPS PIco is as follows:

- Powered from the J8 (P1) connector of the Raspberry Pi® via UPS PIco
- PWM FAN speed regulation
- 1 RED LED based information system (Light Red - hot, No Light Red – cold) placed on the UPS PIco board
- Full control over the system via I2C interface (The PiCO Interface):
- Unconditional Fan ON/OFF
- PWM FAN speed regulation
- Temperature threshold set/get
- Current System Temperature read
- Supports Celsius and Fahrenheit scale

- Can be used inside of the most of already existing cases

Kit Contents:

1. Micro Fan with cable
2. Set of 4 pcs of tree clips required for PIco FAN mounting UPS PIco PCB
3. Set of 4 pcs of rubber washers required for the PIco FAN mounting UPS PIco PCB
4. TO-92 Temperature sensor
5. 2mm PCB connector for the FAN

Case Fitment

The PIco FAN is very low profile, placed on the UPS PIco bottom side, so will fits to most cases.

Assembly Instructions

In order to assemble the PIco Fan Kit a very simple hand work is required. All required parts are contained in the PIco Fan Kit box. However some basic tools are needed:

1. Soldering Station (or simple tool)
2. Cutting Pliers
3. Cutting Blade
4. Tweezers

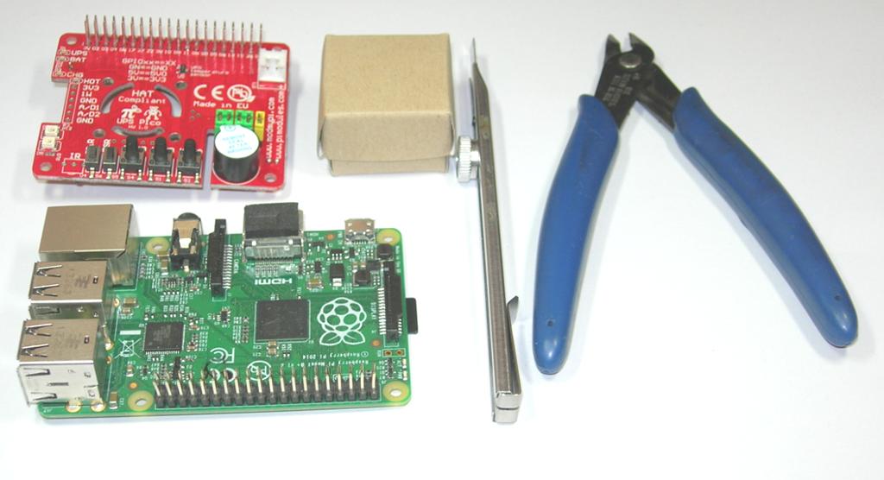
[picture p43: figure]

Figure 1 Tools required for the PIco FAN Kit assembly

The following steps need to done in order to complete setup of the PIco Fan Kit.

Remove all PIco FAN Kit parts from the packing box

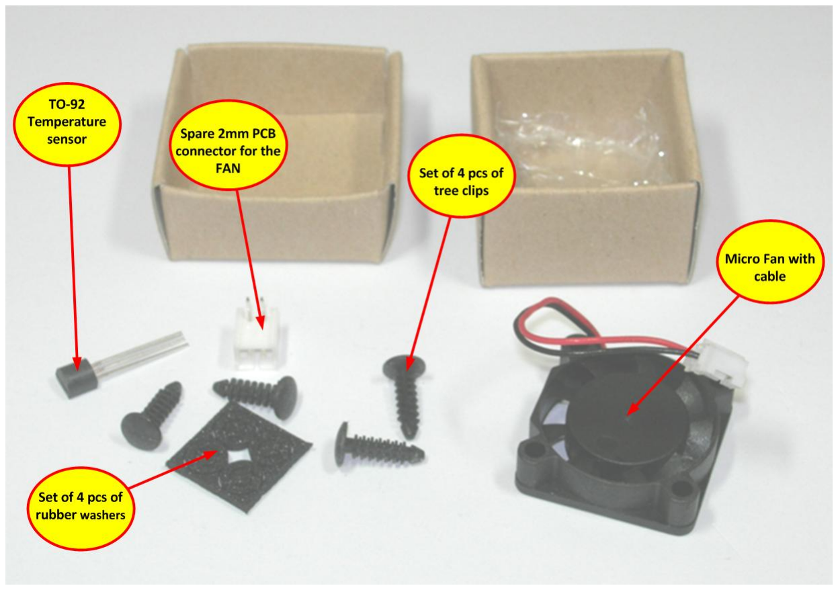
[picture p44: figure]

Figure 2 PIco FAN Kit parts

The above shown in the picture parts should be found in the box. There are:

1. Micro fan with cable
2. Set of 4 pcs of tree clips required for PIco FAN mounting UPS PIco PCB
3. Set of 4 pcs of rubber washers required for the PIco FAN mounting UPS PIco PCB
4. TO-92 Temperature sensor
5. Spare 2mm PCB connector for the FAN

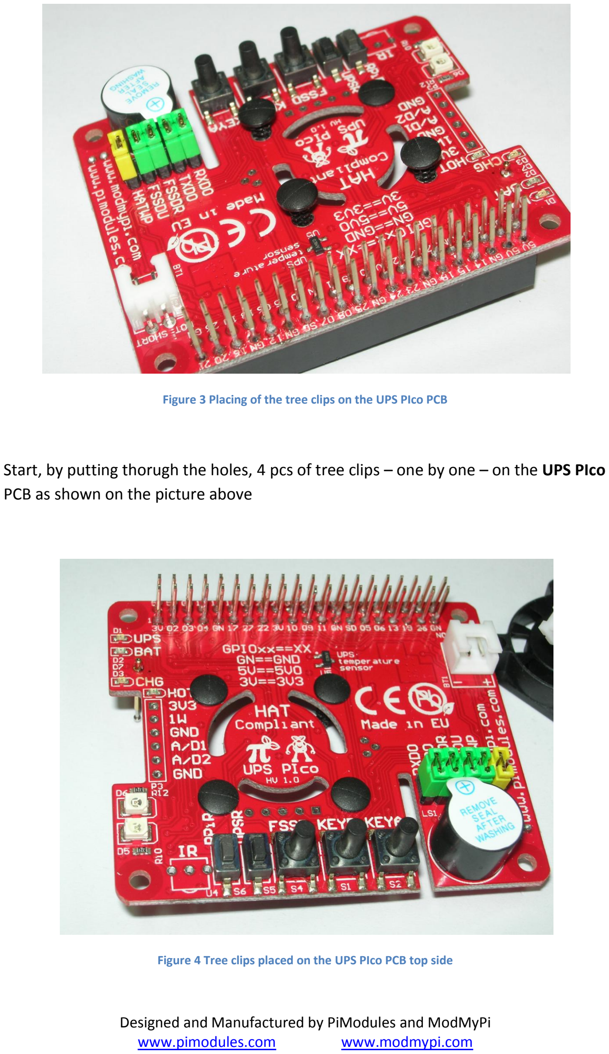
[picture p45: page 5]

Figure 3 Placing of the tree clips on the UPS PIco PCB

Start, by putting thorugh the holes, 4 pcs of tree clips – one by one – on the UPS PIco PCB as shown on the picture above

Figure 4 Tree clips placed on the UPS PIco PCB top side

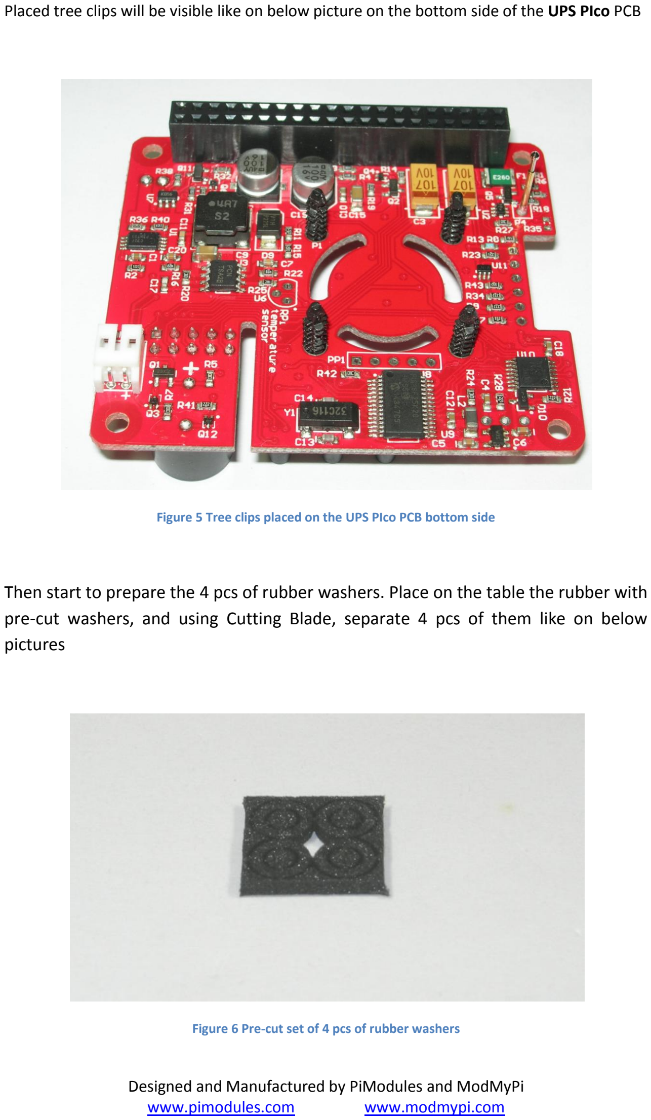
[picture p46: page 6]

Placed tree clips will be visible like on below picture on the bottom side of the UPS PIco PCB

Figure 5 Tree clips placed on the UPS PIco PCB bottom side

Then start to prepare the 4 pcs of rubber washers. Place on the table the rubber with pre-cut washers, and using Cutting Blade, separate 4 pcs of them like on below pictures

Figure 6 Pre-cut set of 4 pcs of rubber washers

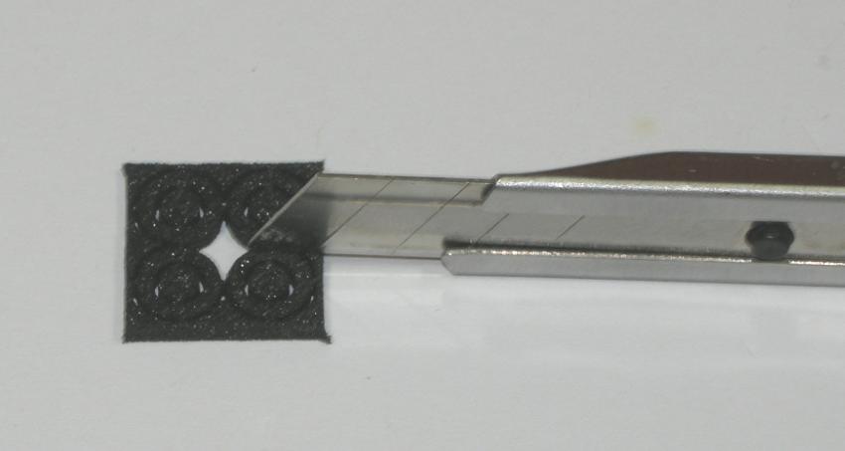
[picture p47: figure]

Figure 7 Cutting out the 4 pcs of rubber washers

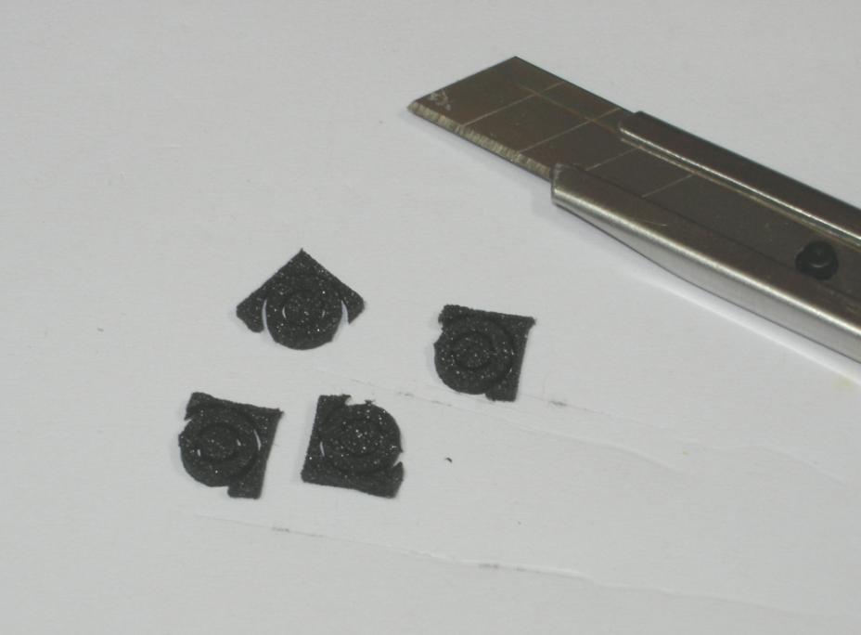
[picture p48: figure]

Figure 8 Rubber washers after partially cut-out

Then, after cut-out of them, using your fingers separate each one from the around rubber. The result will be like on the picture below.

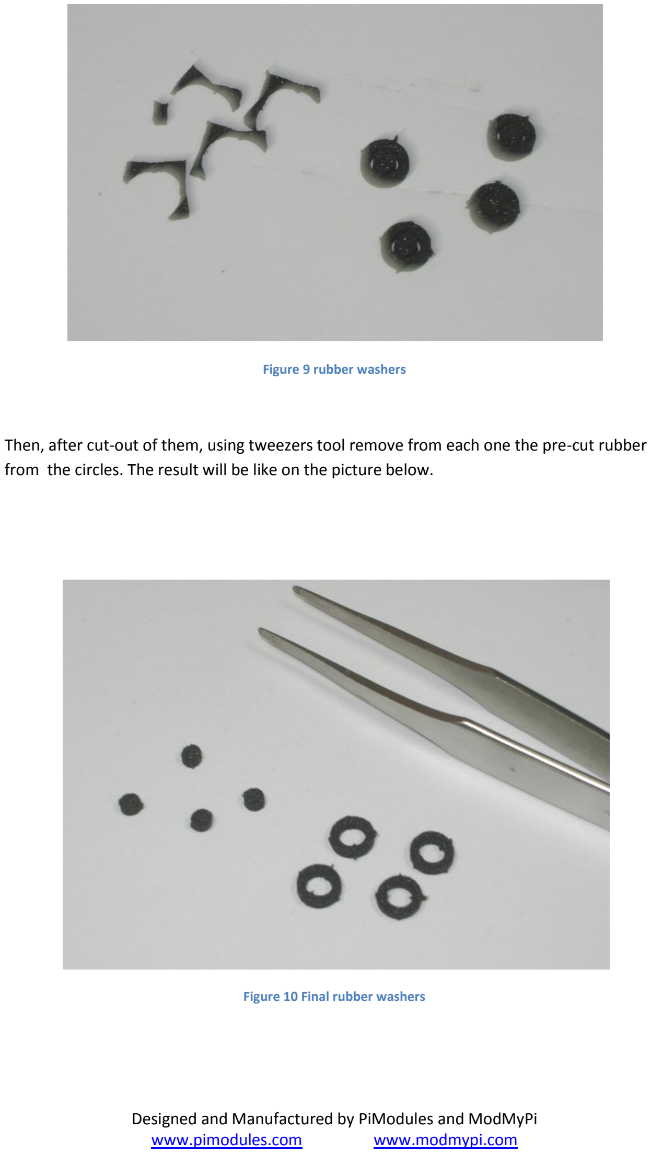
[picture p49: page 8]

Figure 9 rubber washers

Then, after cut-out of them, using tweezers tool remove from each one the pre-cut rubber from the circles. The result will be like on the picture below.

Figure 10 Final rubber washers

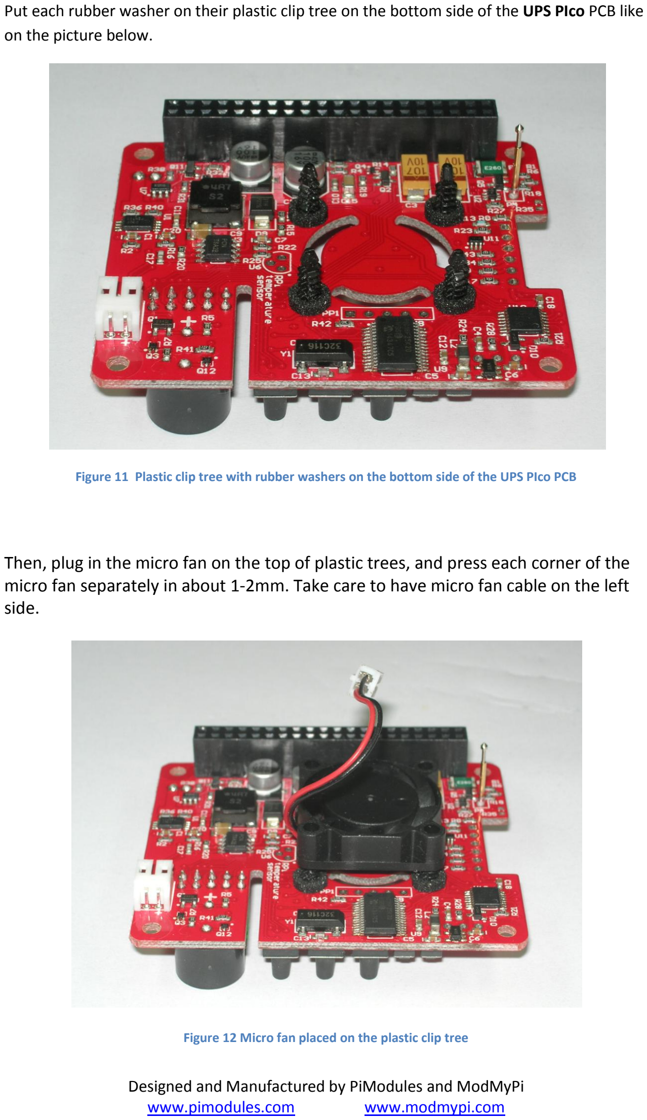
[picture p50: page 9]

Put each rubber washer on their plastic clip tree on the bottom side of the UPS PIco PCB like on the picture below.

Figure 11 Plastic clip tree with rubber washers on the bottom side of the UPS PIco PCB

Then, plug in the micro fan on the top of plastic trees, and press each corner of the micro fan separately in about 1-2mm. Take care to have micro fan cable on the left side.

Figure 12 Micro fan placed on the plastic clip tree

Repeat this task until distance between micro fan and bottom side of the UPS PIco PCB will be around 1-1.5 mm. The rubber washers will be slightly pressed.

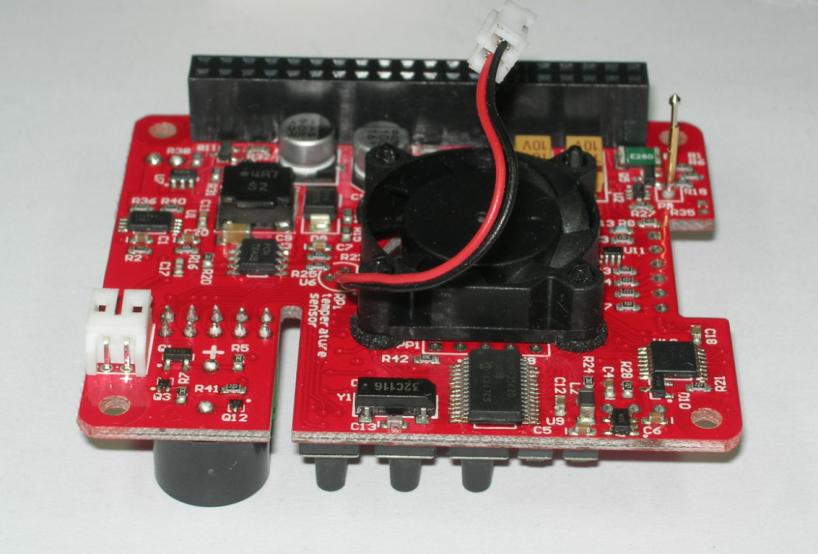
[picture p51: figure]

Figure 13 Micro fan placed on the plastic clip tree with final distance of 1.5mm

Connect the micro fan 2mm connector to the plug placed on the bottom side of the UPS PIco PCB

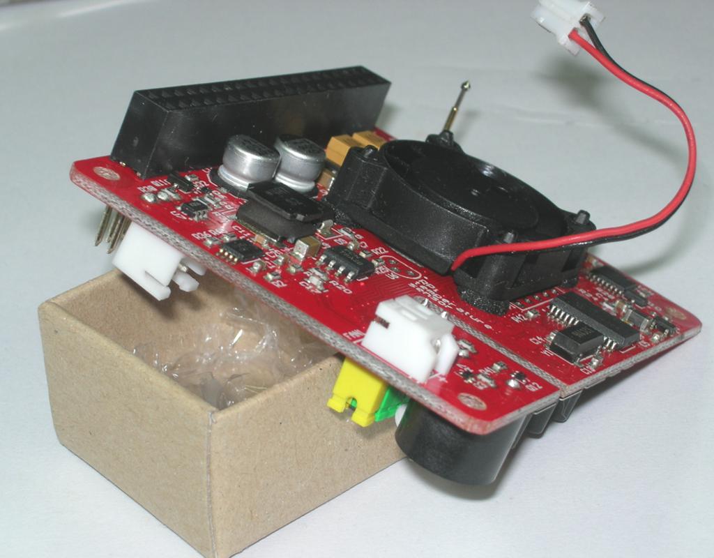
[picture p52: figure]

Figure 14 Micro fan placed on the UPS PIco PCB ready to connect

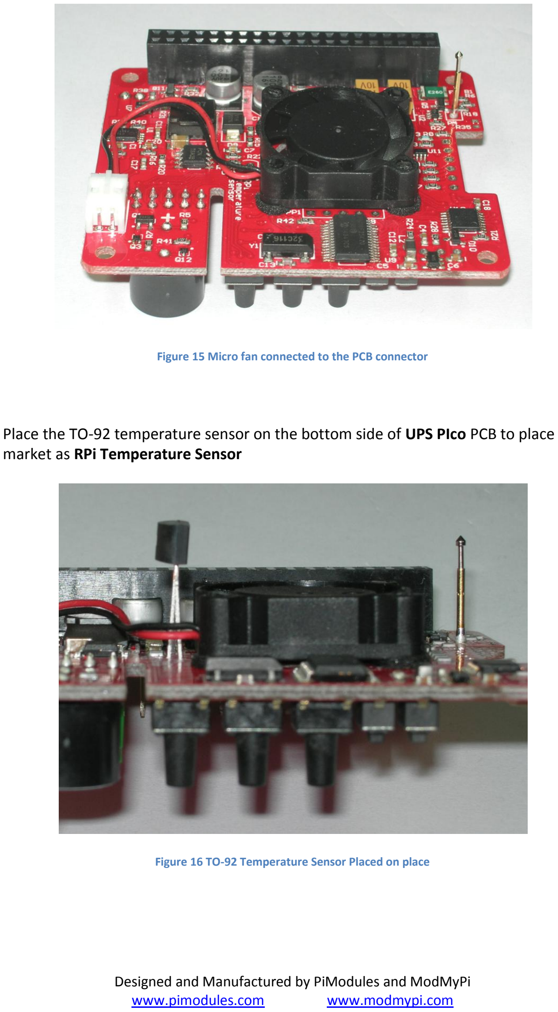
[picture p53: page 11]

Figure 15 Micro fan connected to the PCB connector

Place the TO-92 temperature sensor on the bottom side of UPS PIco PCB to place market as RPi Temperature Sensor

Figure 16 TO-92 Temperature Sensor Placed on place

Put the completed UPS PIco PCB with fan and TO-92 Temperature Sensor on the top of Raspberry Pi®. With one finger press the pins of the TO-92 Temperature Sensor in order to make it touching the Raspberry Pi®.

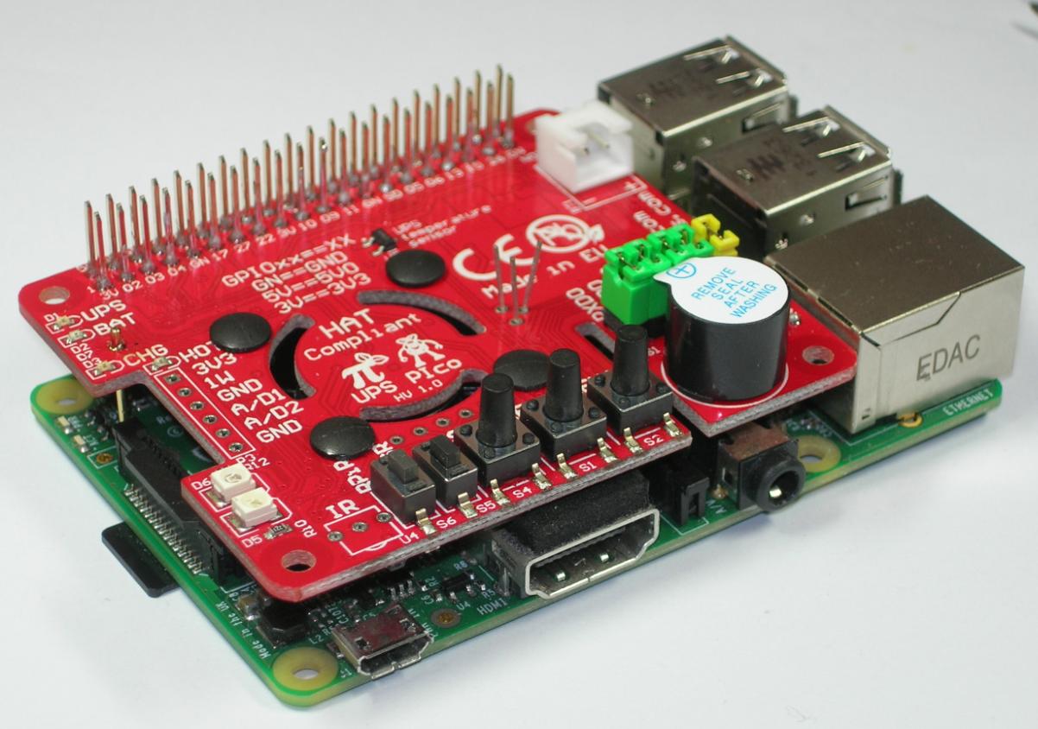
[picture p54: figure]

Figure 17 UPS PIco with fan and TO-92 Temperature Sensor Placed on the Raspberry Pi®

With your finger press the pins of the TO-92 Temperature Sensor in order to make it touching the Raspberry Pi® pcb.

With a soldering tool solder thir pins to the UPS PIco pcb and cut the remain pins.

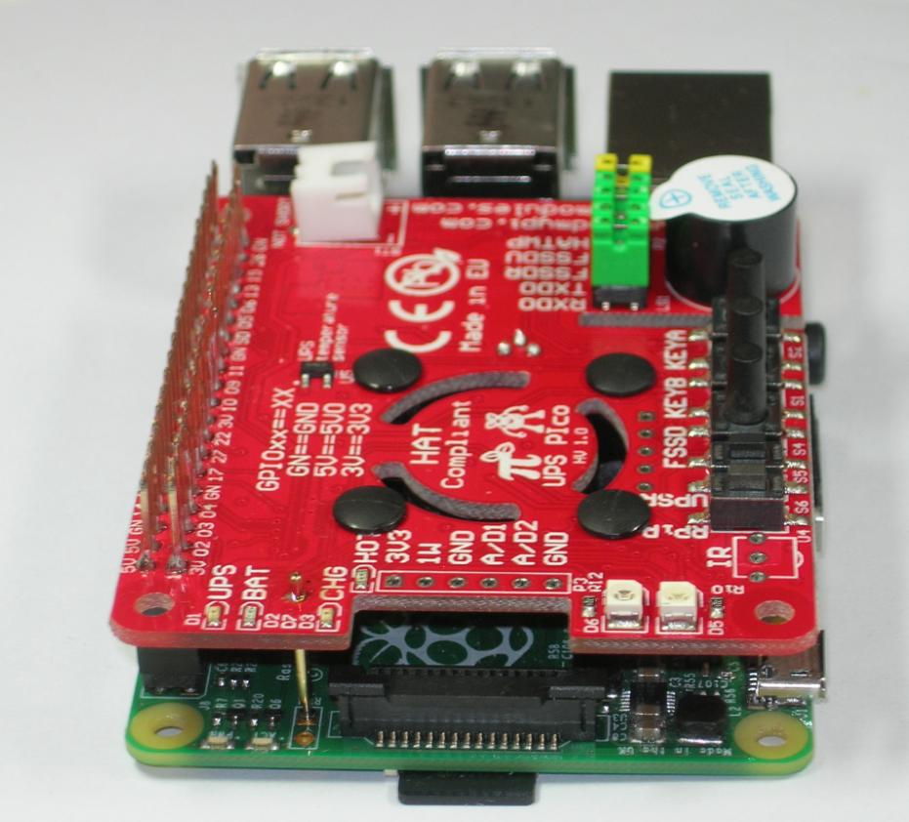
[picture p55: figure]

Figure 18 UPS PIco with fan and TO-92 Temperature Sensor assembled ready to be used

Your PIco FAN Kit is assembled and ready to be used. It will cool the Raspberry Pi® PCB, the Raspberry Pi® processor as also the UPS PIco.

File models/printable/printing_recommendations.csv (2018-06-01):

filename | wall_thickness | color | infill_percent | platform_adhesion | support_type | obsolete
arduino_tray_2_20160508.stl | 0.8 |  |  |  |  | 0
ballast_tray_20160414.stl | 0.8 |  |  |  |  | 0
battery_holder_18659_x3.stl |  |  |  |  |  | 0
battery_tray2_cartridge_bottom_20160522.stl | 0.8 |  |  |  |  | 0
battery_tray2_cartridge_top_20160522.stl | 0.8 |  |  |  |  | 0
battery_tray2_nub_20160522.stl | 0.8 |  |  | brim |  | 0
battery_tray2_receiver_20160522.stl | 0.8 |  |  |  |  | 0
battery_tray3_cartridge_bottom.stl |  |  |  |  |  | 0
battery_tray3_cartridge_top.stl |  |  |  |  |  | 0
battery_tray3_holder.stl |  |  |  |  |  | 0
battery_tray3_support.stl |  |  |  |  |  | 0
bearings_slew_bearing_inner_bottom_20160214.stl | 0.8 |  |  |  |  | 0
bearings_slew_bearing_inner_top_20160214.stl | 0.8 |  |  |  |  | 0
bearings_slew_bearing_outer_20160214.stl | 0.8 | black | 15 |  |  | 0
bearings_slew_bearing_outer_mount_20160215.stl | 0.8 |  |  |  |  | 0
bnO055_mount.stl |  |  |  |  |  | 0
caster_housing_bottom.stl |  |  |  |  |  | 0
caster_housing_center.stl |  |  |  |  |  | 0
caster_housing_top.stl |  |  |  |  |  | 0
caster_housing_wheel.stl |  |  |  |  |  | 0
caster_housing_wheel_d10.stl |  |  |  |  |  | 0
caster_housing_wheel_d11.stl |  |  |  |  |  | 0
collar_front.stl | 0.8 |  |  |  |  | 0
collar_side.stl | 0.8 |  |  |  |  | 0
commotion_switch.stl |  |  |  |  |  | 0
conduit_beam_20151108.stl | 0.8 |  |  |  |  | 0
dc_converter_tray_20150917.stl | 0.8 |  |  |  |  | 0
dock_mast_recessor.stl |  |  |  |  |  | 0
dock_masthead.stl |  |  |  |  |  | 0
dock_retainer.stl |  |  |  |  |  | 0
dock_rim_part1.stl |  |  |  |  |  | 0
dock_rim_part2.stl |  |  |  |  |  | 0
dock_rim_part3.stl |  |  |  |  |  | 0
dock_rim_part4.stl |  |  |  |  |  | 0
dock_rim_part5.stl |  |  |  |  |  | 0
edge_sensor_mount_20151110.stl | 0.8 |  |  |  |  | 0
edge_sensor_mount_cover_20151111b.stl | 0.8 |  |  |  |  | 0
flexiTreads_driver_20150801.stl | 0.8 |  |  |  |  | 0
flexiTreads_idler.stl | 0.8 |  |  |  |  | 0
flexiTreads_tensioner_18_10_20160529.stl | 0.8 |  | 15 |  |  | 0
flexiTreads_track_sprockets12_length228_20150920.stl | 0.8 |  |  |  |  | 0
gears_pan_gears_small_dh_20150906.stl | 0.8 |  |  |  |  | 0
head_arduino_mount_20171120.stl |  |  |  |  |  | 0
head_bottom.stl | 0.8 |  |  |  |  | 0
head_face_laser_mount_20160214.stl | 0.8 |  |  |  |  | 0
head_face_led_mount_20160214.stl | 0.8 |  |  |  |  | 0
head_face_sensor_mount_20160214.stl | 0.8 |  |  |  |  | 0
head_fan_shroud.stl |  |  |  |  |  | 0
head_front.stl | 0.8 |  |  |  |  | 0
head_power_mount_bottom_20151227.stl | 0.8 |  |  |  |  | 0
head_power_mount_top_20151227.stl | 0.8 |  |  |  |  | 0
head_power_strip_housing_20151211.stl | 0.8 |  |  |  |  | 0
head_power_strip_housing_20151227.stl | 0.8 |  |  |  |  | 0
head_shell_back.stl | 0.8 |  |  | brim |  | 0
head_shell_back_lower.stl | 0.8 |  |  | brim |  | 0
head_shell_back_lower_tabbed.stl | 0.8 |  |  |  |  | 0
head_shell_front.stl | 0.8 |  |  | brim |  | 0
head_shell_front_lower.stl | 0.8 |  |  |  |  | 0
head_shell_front_lower_tabbed.stl | 0.8 |  |  |  |  | 0
head_shell_front_middle.stl | 0.8 |  |  |  | touching | 0
head_shell_side_bottom.stl | 0.8 |  |  | brim |  | 0
head_shell_side_top.stl | 0.8 |  |  | brim |  | 0
head_shell_top.stl | 1.2 |  | 15 |  |  | 0
head_shell_top_tabbed.stl | 0.8 |  |  |  |  | 0
head_strut_open_side.stl | 0.8 |  |  |  |  | 0
head_strut_servo_side.stl | 0.8 |  |  |  |  | 0
head_top.stl | 0.8 |  |  |  |  | 0
head_wire_through_a.stl | 0.8 |  |  |  |  | 0
head_wire_through_b.stl | 0.8 |  |  |  |  | 0
horizontal_20150726.stl | 0.8 |  |  |  |  | 0
horizontal_motor_top_slotted_20150915.stl | 0.8 |  |  |  |  | 0
horizontal_mount_20150816.stl | 0.8 |  |  |  |  | 0
lower_rear_panel_20151122.stl | 0.8 |  |  |  |  | 0
lrf_calibration_base.stl | 0.8 |  |  |  |  | 0
lrf_calibration_base_75d.stl | 0.8 |  |  |  |  | 0
lrf_calibration_centerpoint.stl | 0.8 |  |  |  |  | 0
lrf_calibration_nub.stl | 0.8 |  |  |  |  | 0
lrf_calibration_nub_all.stl | 0.8 |  |  |  |  | 0
lrf_calibration_top.stl | 0.8 |  |  |  |  | 0
mic_mount.stl | 0.8 |  |  |  |  | 0
mock_tread.stl | 0.8 |  |  |  |  | 0
motor_gear_drive.stl |  |  |  |  |  | 0
motor_mount_pan_bottom_20151224.stl | 0.8 |  |  |  |  | 0
motor_mount_pan_top_20151224.stl | 0.8 |  |  |  |  | 0
motor_pan_driver_mount.stl | 0.8 |  |  |  |  | 0
motor_unimount_2_a0_20160406.stl | 0.8 |  |  |  |  | 0
motor_unimount_2_b0_20160406.stl | 0.8 |  |  |  |  | 0
motor_wheel_axle.stl |  |  |  |  |  | 0
motor_wheel_plate_inner.stl |  |  |  |  |  | 0
motor_wheel_plate_outer.stl |  |  |  |  |  | 0
motor_wheel_wheel.stl |  |  |  |  |  | 0
mpu6050_mount_20160508.stl | 0.8 |  |  |  |  | 0
neck_sensor_mount.stl |  |  |  |  |  | 0
neck_strut_open.stl | 0.8 |  |  |  |  | 0
neck_strut_servo.stl | 0.8 |  |  |  |  | 0
neck_strut_servo_mount_20150928.stl | 0.8 |  |  |  |  | 0
power_switch_holster_20151120.stl | 0.8 |  |  |  |  | 0
power_switch_mount_20151120.stl | 0.8 |  |  |  |  | 0
qrd1114_mount_a_20151205a.stl | 0.8 |  |  |  |  | 0
qrd1114_mount_b_20151205b.stl | 0.8 |  |  |  |  | 0
recharge_plug_female_v2_20160519.stl | 0.8 |  |  |  |  | 0
recharge_plug_male_20151127c.stl | 0.8 |  |  |  |  | 0
rpi_tray2.stl | 0.8 |  |  |  |  | 0
screw_2p5_10.stl | 0.8 |  |  |  |  | 0
screw_terminal_4_20160524.stl | 0.8 |  |  |  |  | 0
screw_terminal_4_flipped_20160524.stl | 0.8 |  |  |  |  | 0
screw_terminal_6_20151121b.stl | 0.8 |  |  |  |  | 0
screws_2p5_15.stl | 0.8 |  |  |  |  | 0
screws_2p5_20.stl | 0.8 |  |  |  |  | 0
side_frame_extension_20151129.stl | 0.8 |  |  |  |  | 0
side_panel_20151204b.stl | 0.8 |  |  |  |  | 0
sonar_mount_2015119.stl | 0.8 |  |  |  |  | 0
speaker_mount_20160503.stl | 0.8 |  |  |  |  | 0
speaker_mount_a.stl | 0.8 |  |  |  |  | 0
speaker_mount_b.stl | 0.8 |  |  |  |  | 0
spiral_spring_samples.stl | 0.8 |  |  |  |  | 0
spring_test.stl | 0.8 |  |  |  |  | 0
top_front_panel_20151122.stl | 0.8 |  |  |  |  | 0
top_front_panel_door_20151122.stl | 0.8 |  |  |  |  | 0
top_rear_panel2_20160526.stl | 0.8 |  |  |  |  | 0
top_rear_panel2_button_20160526.stl | 0.8 |  |  |  |  | 0
torso_head_jack_bottom.stl | 0.8 |  |  |  |  | 0
torso_head_jack_top.stl | 0.8 |  |  |  |  | 0
torso_wire_restrainer.stl | 0.8 |  |  |  |  | 0
vertical_20150726.stl | 0.8 |  |  |  |  | 0
vertical_back_slotted_20150916.stl | 0.8 |  |  |  |  | 0
vertical_battery_slotted_20150915.stl | 0.8 |  |  |  |  | 0
vertical_slotted_20150915.stl | 0.8 |  |  |  |  | 0

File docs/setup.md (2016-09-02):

Software Setup
==============

Structure
---------

Configuring your robot will require two computers. The first is the Raspberry Pi physically located on the robot. The second is the deployment machine, where the robot's base code and configuration will be managed from and eventually deployed to the Raspberry Pi. Both computers are assumed to be running Linux.

Configuring the Deployment Machine
----------------------------------

Assuming your deployment machine is one you're reading this documentation from, your localhost, start by checking out this project via git. Open a terminal in a directory where you keep your Git projects and run:

    git clone https://github.com/chrisspen/homebot.git

Initialize your deployment environment by running:

    ./bootstrap

This command creates a Python virtual environment and installs a few required packages.

Note, any command presented in this guide beginning with "fab" should be run in a terminal from the project's root directory. Also, that terminal must first have your virtual environment activated by running:

    . ./setup.bash

Set your custom settings by running:

    cp roles/local/settings_local.yaml.template roles/local/settings_local.yaml

By default, it's assumed your deployment machine is running Ubuntu 16.04. Edit this file to select a different OS.
    
Next, install ROS by running:

    . ./setup.bash
    fab local ros.configure

New Install Checklist
---------------------

Decide on the hostname for your robot. For all intents and purposes, the robot will function like a Linux server

1. Ensure you've purged the domain name from your local router's DHCP cache, or it could interfere with the install.

    $ ping <domain>
    ping: unknown host <domain>
    
2. Purge all old SSH keys:

     fab prod host.purge_keys

Installing the Operating System
-------------------------------

1. Set your custom settings by running:

    cp roles/prod/settings_local.yaml.template roles/prod/settings_local.yaml
    
This file represents your custom software configurations to the robot and will override any defaults.

Edit the values in this file to suite your preferences. At the very least, you'll need to specify your wifi SSID and password so you can access the robot remotely.

2. Insert an SD card into the card reader on your deployment machine and run:

    fab local rpi.init_raspbian_disk
    
3. Insert card into Pi and power on.

4. Begin installation using:

    fab prod deploy.run
    
Note, this may take up to 5 hours to complete.

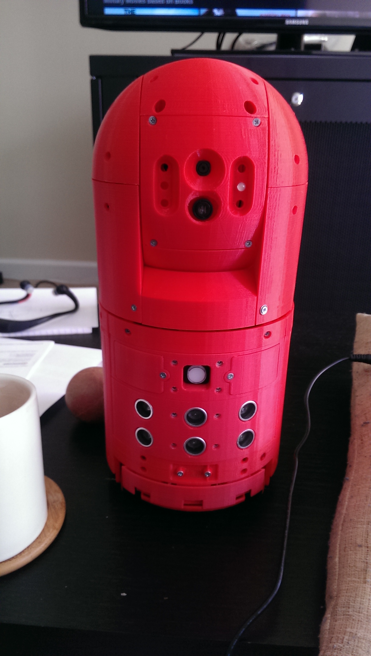
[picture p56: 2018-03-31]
docs/img/bot/assembled_complete_20160612_105319.jpg

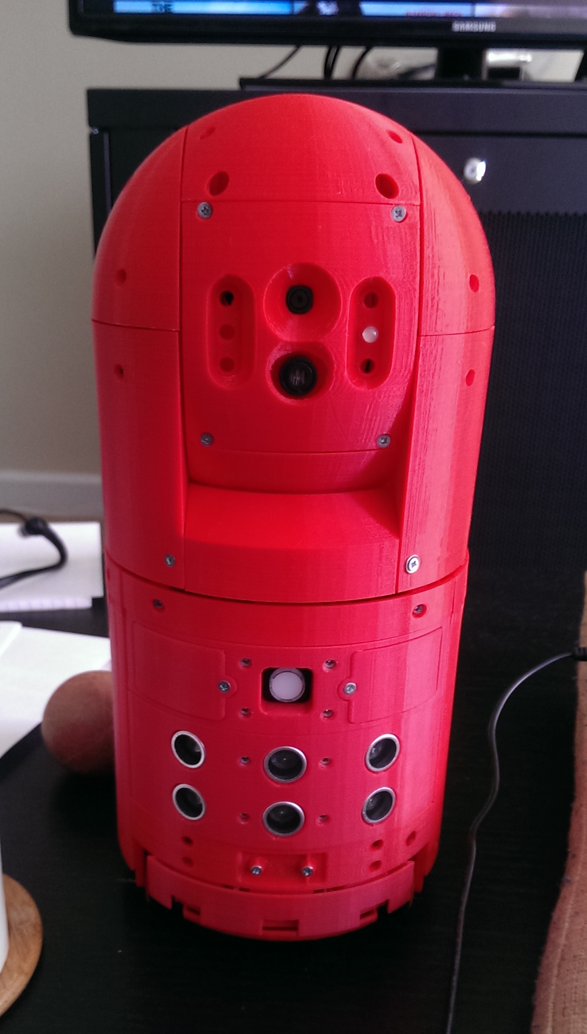
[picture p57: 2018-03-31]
docs/img/bot/assembled_complete_20160612_105319-cropped.jpg

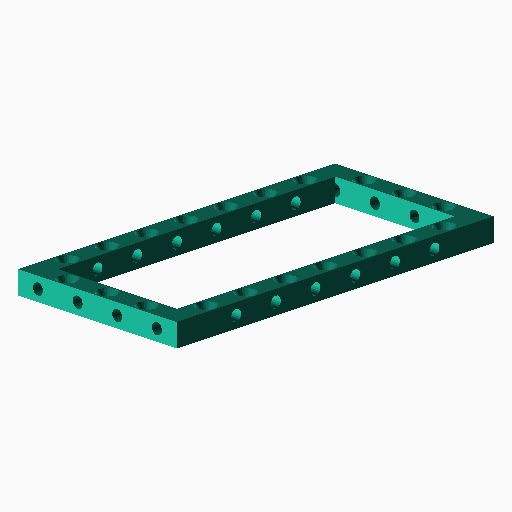
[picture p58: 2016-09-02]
models/printable/vertical_20150726.png

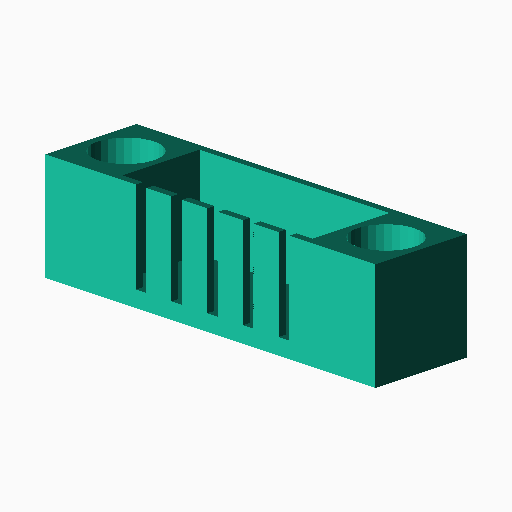
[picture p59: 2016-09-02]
models/printable/head_power_strip_housing_20151211.png

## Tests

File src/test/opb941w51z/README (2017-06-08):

A test for the wiring for hte OPB941 sensor.

This is very similar in concept to the wiring for the QRD1114.

Build by running:

    make
    make upload
    make monitor

Function:

    When the slotted sensor is obstructed, the signal will read LOW.
    When unobstructed (clear), the signal will read HIGH.

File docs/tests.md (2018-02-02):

Tests
=====

These are tests for evaluating milestones and basic functionality. They are listed roughly in order of dependence. A test at the end usually requires passing one of the earlier tests.

Collision avoidance
-------------------

Moves the platform forward at 25% speed until an obstacle is detected via ultrasonic, at which point it should immediately halt before colliding.

    rosrun ros_homebot motion.py
    rosrun ros_homebot forward_client.py

Edge avoidance
--------------

Move the platofrm foward at 25% speed until an edge or cliff is detected, at which point it should immediately halt before falling.

    rosrun ros_homebot motion.py
    rosrun ros_homebot forward_client.py

QR tracking
-----------

Search for and track a QR code using the head camera. Head should pan and tilt to track code as it moves.

    rosrun ros_homebot track_qr.py

QR following
------------

Search for and track a QR code, maintaining a fixed distance from the code at all times. This is meant to be tested on a treadmill, where the QR code is mounted at the front of the treadmill facing the robot, with the speed slowly being increased from 0mph to 1-2mph. The robot should be able to proportionally increase it's speed and adjust drift to keep itself centered in the middle of the treadmill width-wise and at a relatively fixed distance roughly in the middle length-wise. 

    rosrun ros_homebot treadmill.py

Auto docking
------------

The docking station, identified with a unique QR code, is placed within eyesight of the robot. The robot should then identify the docking station, and manuver itself into docking position so that it begins recharging.

    todo

SLAM
----

Map and localize itself within one or more rooms. After mapping is complete, a room will be specified on a map, and the robot should be able to autonomously navigate to that room.

    todo

Kidnapped
---------

After mapping a small group of rooms, the robot will be deactivated, manually relocated to a different room, and then reactivated, at which point it will have to navigate to the original room it was in.

    todo

Baby duck
---------

Identify and track a target as they move around.

    todo

Hide and go seek
----------------

Identify target's face and body pattern, and then deactivate camera and count to 10 while target moves to a different location. At the end of the countdown, robot will then begin searching for the person, stopped when the person is identified. The rooms should be mapped as it travels so areas are not redundently searched unless necessary.

    todo

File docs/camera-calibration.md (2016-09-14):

Camera Calibration
==================

Calibrating the Raspberry Pi camera module
------------------------------------------

To calibrate the Raspberry Pi camera module, start by running the camera node on the Pi with:

    roslaunch ros_homebot raspicam_raw.launch

Then, on your deployment machine, initialize your shell with:

    . src/ros/setup.bash
    export ROS_MASTER_URI=http://robot.local:11311
    
Ensure you deployment machine can access the camera stream by running:

    rosrun image_view image_view image:=/raspicam/image _image_transport:=compressed

You should see a small window showing the camera stream with very high (3-6 second) latency.

Close this window by focussing the terminal and pressing ctrl+c.

Then run the [ROS monocular calibration script](http://wiki.ros.org/camera_calibration/Tutorials/MonocularCalibration) with:

    rosrun camera_calibration cameracalibrator.py --size 8x6 --square 0.025 image:=/camera/image camera:=/camera --no-service-check --camera_name=raspicam

Move the checkerboard pattern around in front of the camera, going slowly to ensure the calibration script can identify the pattern, indicated by showing an overlay of colored lines between the checkerboard vertices. Slowly move the checkerboard left, right, up and down, tilting it forwards and backwards, close to the camera and then farther away from the camera. When enough data has been collected, the lines on the right hand side of the screen should turn blue and the "Calibrate" button should highlight. Click it once, then click "Save", and then exit the window.

Note, the "Commit" button attempts to send the calibration parameters directly to the camera node via a service call. However, this is not supported, so it will only throw an error in the console.

The calibration data will be printed to the console. It will also be saved to a file at /tmp/calibrationdata.tar.gz.

Extract the file `ost.yaml` from calibrationdata.tar.gz and copy it to raspicam_node/calibrations/camera.yaml.

Push the new file to the Pi and test the new calibration by running on the Pi:

    roslaunch ros_homebot raspicam_compressed_320.launch

Confirm the compressed video feed looks correct by viewing it from your deployment machine with:

    rosrun image_view image_view image:=/camera/image _image_transport:=compressed

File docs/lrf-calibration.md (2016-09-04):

Laser Range Finder Calibration
==============================

Ensure the Raspberry Pi camera module is first calibrated.

Leveling
--------

To begin the laser range finder (LRF) calibration, begin by ensuring the line laser is level relative to the camera. Since distance is calculated based on the laser's vertical position in the image, it's important that the line laser is equally level throughout the image. A laser reading close to the center of the image will be interpreted as an object far away, whereas a reading close to the bottom of the imaeg will be interpreted as an object close by. If the laser is tilted relative to the camera, then a flat wall perfectly perpendicular to the camera may be interpreted nonsensically as being both very close and almost infinitely far away.

Face the platform at a flat wall, about 50 cm away, with no obstructions. Then run on the Pi:

    roslaunch ros_homebot raspicam_compressed_320.launch
    roslaunch ros_homebot rpi_gpio.launch

and from your deployment machine, run:

    roslaunch ros_homebot lrf_straightener.launch

This will sample the laser readings and calculate the variance in the vertical position of the laser in the camera image. If the variance is 0, the laser is perfectly aligned. The variance should be no more than 10. If the reading is more than this, assure you're oriented the platform properly (if the wall is not flat or there are obstructions, false readings will occur) and that the line laser is level. Gently twist the line laser and re-run the process until a low variance is reported.

Calibration
-----------

Next we'll associate the raw line laser readings with real-world distance measurements.

Begin by setting up 6 distance markers evenly around the platform within the 90 degree view of the camera. Use strings of known lengths ranging from:

* 5cm
* 10cm
* 50cm
* 100cm
* 200cm
* 300cm

Activate the line laser with:

    rosservice call /rpi_gpio/set_pin 20 1

Confirm the line laser shines equally across all marker labels, then deactivate the line laser with:

    rosservice call /rpi_gpio/set_pin 20 0

Then run:

    rosrun ros_homebot_lrf lrf_node.py _marker:=1

This will display a window showing an image of the line laser. Follow the on-screen instructions.

Finally, confirm calibration has been set correctly but running a continuous laser ranger finder with:

    export ROS_MASTER_URI=http://robot.local:11311
    roslaunch ros_homebot lrf_compressed_320_debug.launch

and visualizing it with:

    export ROS_MASTER_URI=http://robot.local:11311
    rosrun ros_homebot_lrf lrf_plot.py

Slowly move your hand in front of the laser and confirm the visualization changes accordingly.

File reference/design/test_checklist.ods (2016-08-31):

Test | Parts
Motors | forward,reverse,left,right
Edge Sensors | left,center,right
Bumper Sensors | left,center,right
Ultrasonic Sensors | left,center,right
External Power | on,off
Battery Voltage
Accel/Gyro

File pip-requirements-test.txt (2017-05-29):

mkdocs==0.16.1
mkdocs-bootstrap==0.1.1
tox==2.6.0
pylint<1.7
cpplint==1.3.0
burlap==0.9.2

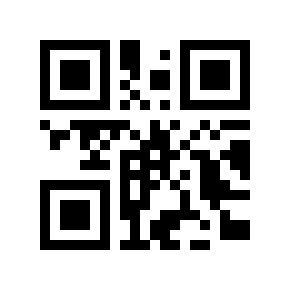
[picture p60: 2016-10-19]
src/test/treadmill/images/test-pure-Some text.jpg

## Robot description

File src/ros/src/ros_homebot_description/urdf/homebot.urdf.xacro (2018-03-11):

<?xml version="1.0" encoding="UTF-8"?>
<!--
This is loaded by robot_state_publisher and used to calculate poses from odometry and joint messages.
-->
<robot xmlns:xacro="http://www.ros.org/wiki/xacro" name="homebot">
    <xacro:include filename="$(find ros_homebot_description)/urdf/materials.urdf.xacro" />
    <!-- dimensions in meters -->
    <xacro:property name="torso_radius" value="0.075" /><!-- 150 mm diameter = 75 mm radius -->
    <xacro:property name="torso_height" value="0.16" /><!-- 160 mm height -->
    <xacro:property name="neck_height" value="0.015" />
    <xacro:property name="camera_radius" value="0.008" />
    <xacro:property name="camera_thickness" value="0.005" />
    <xacro:property name="M_PI" value="3.141592653589793" />
    
    <!--
    <link name="base_footprint">
        <visual>
            <origin xyz="0 0 0" rpy="0 0 0" />
            <geometry>
                <box size="0.001 0.001 0.001" />
            </geometry>
        </visual>
        <inertial>
            <mass value="0.0001" />
            <origin xyz="0 0 0" />
            <inertia ixx="0.0001" ixy="0.0" ixz="0.0" iyy="0.0001" iyz="0.0" izz="0.0001" />
        </inertial>
    </link>
    -->
    
    <link name="base_link">
        <visual>
            <geometry>
                <cylinder length="${torso_height}" radius="${torso_radius}" />
            </geometry>
            <origin xyz="0 0 ${torso_height/2}" rpy="0 0 0" />
            <material name="red" />
        </visual>
    </link>
    
    <link name="imu">
        <visual>
            <geometry>
                <box size=".03 .015 .01" />
            </geometry>
            <origin xyz="0 0 0" rpy="0 0 0" />
            <material name="orange" />
        </visual>
    </link>
    
    <link name="neck">
        <visual>
            <geometry>
                <cylinder length="${neck_height}" radius="${torso_radius}" />
            </geometry>
            <origin xyz="0 0 ${neck_height/2}" rpy="0 0 0" />
            <material name="green" />
        </visual>
    </link>
    
    <link name="head">
        <visual>
            <geometry>
                <sphere radius="${torso_radius}" />
            </geometry>
            <origin xyz="0 0 0" rpy="0 0 0" />
            <material name="blue" />
        </visual>
    </link>
    
    <link name="camera">
        <visual>
            <geometry>
                <cylinder length="${camera_thickness}" radius="${camera_radius}" />
            </geometry>
            <origin xyz="0 0 0" rpy="0 90 0" />
            <material name="black" />
        </visual>
    </link>
    
    <!--
    <joint name="footprint_to_base_link_joint" type="fixed">
        <parent link="base_footprint" />
        <child link="base_link" />
        <origin xyz="0 0 0" rpy="0 0 0" />
    </joint>
    -->
    
    <joint name="base_link_to_neck_joint" type="continuous">
        <parent link="base_link" />
        <child link="neck" />
        <origin xyz="0 0 ${torso_height+neck_height}" rpy="0 ${M_PI} 0" />
        <!--<origin xyz="0 0 ${torso_height}" rpy="0 ${M_PI} 0" />-->
        <axis xyz="0 0 1" />
    </joint>
    
    <joint name="base_link_to_imu" type="fixed">
        <parent link="base_link" />
        <child link="imu" />
        <origin xyz="0 ${torso_radius - .015} ${torso_height - .01}" rpy="0 0 0" />
    </joint>
    
    <joint name="neck_to_head_joint" type="revolute">
        <parent link="neck" />
        <child link="head" />
        <origin xyz="0 0 ${-(torso_radius)}" rpy="${M_PI/2} 0 ${M_PI}" />
        <axis xyz="1 0 0" />
        <!-- Should match TILT_MIN/TILT_MAX in ros_homebot_python/constants.py -->
        <limit lower="${(90-65)*M_PI/180}" upper="${(90+65)*M_PI/180}" effort="50" velocity="1"/>
    </joint>
    
    <joint name="head_to_camera_joint" type="fixed">
        <parent link="head" />
        <child link="camera" />
        <origin xyz="0 ${torso_radius} 0" rpy="0 0 0" />
    </joint>
    
    <!--
    <gazebo reference="base_footprint">
        <turnGravityOff>false</turnGravityOff>
    </gazebo>
    <gazebo reference="base_link">
        <material>Gazebo/Red</material>
        <turnGravityOff>false</turnGravityOff>
    </gazebo>
    <gazebo>
        <plugin name="gazebo_ros_control" filename="libgazebo_ros_control.so">
            <robotNamespace>/homebot</robotNamespace>
        </plugin>
    </gazebo>
    -->
</robot>

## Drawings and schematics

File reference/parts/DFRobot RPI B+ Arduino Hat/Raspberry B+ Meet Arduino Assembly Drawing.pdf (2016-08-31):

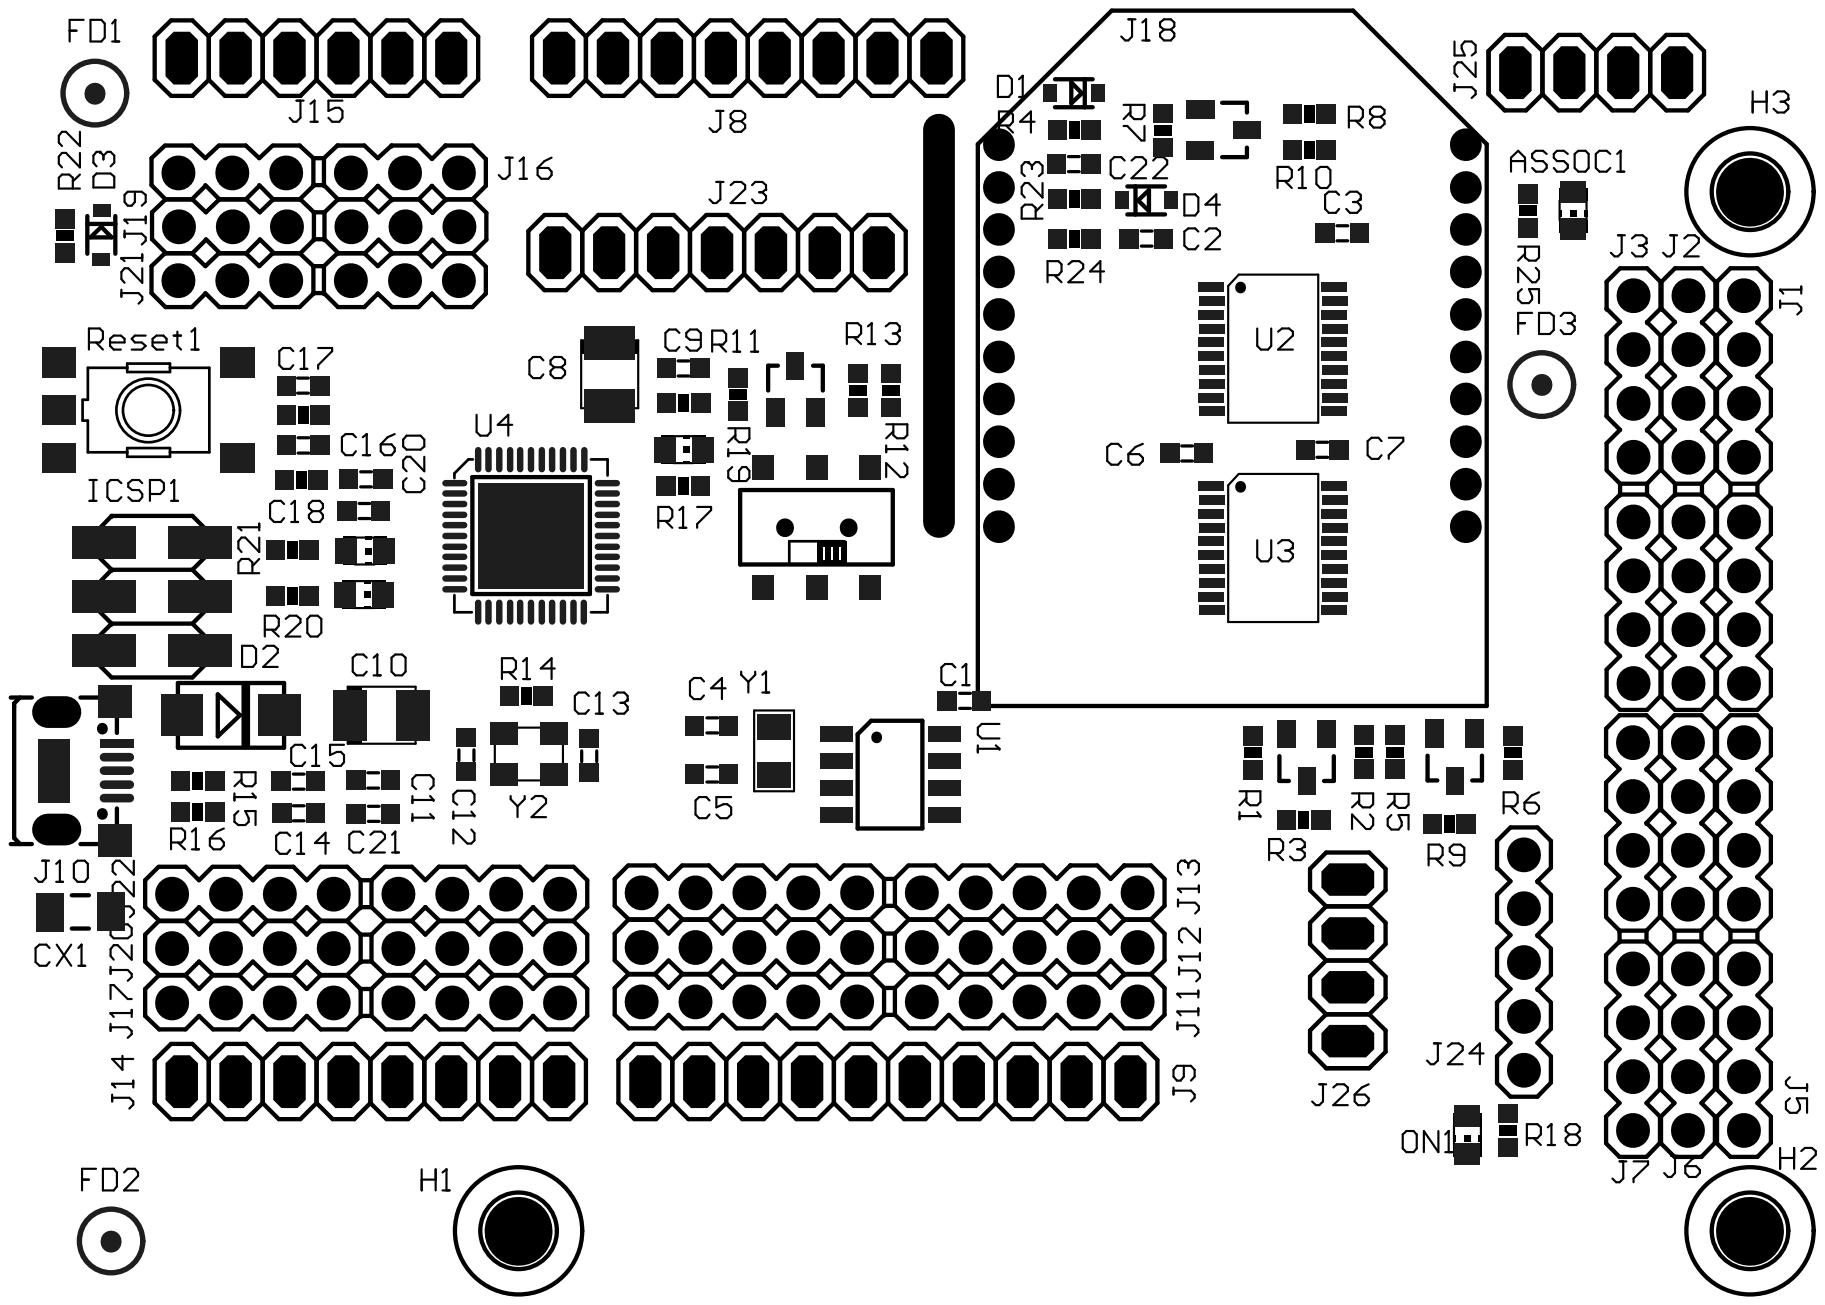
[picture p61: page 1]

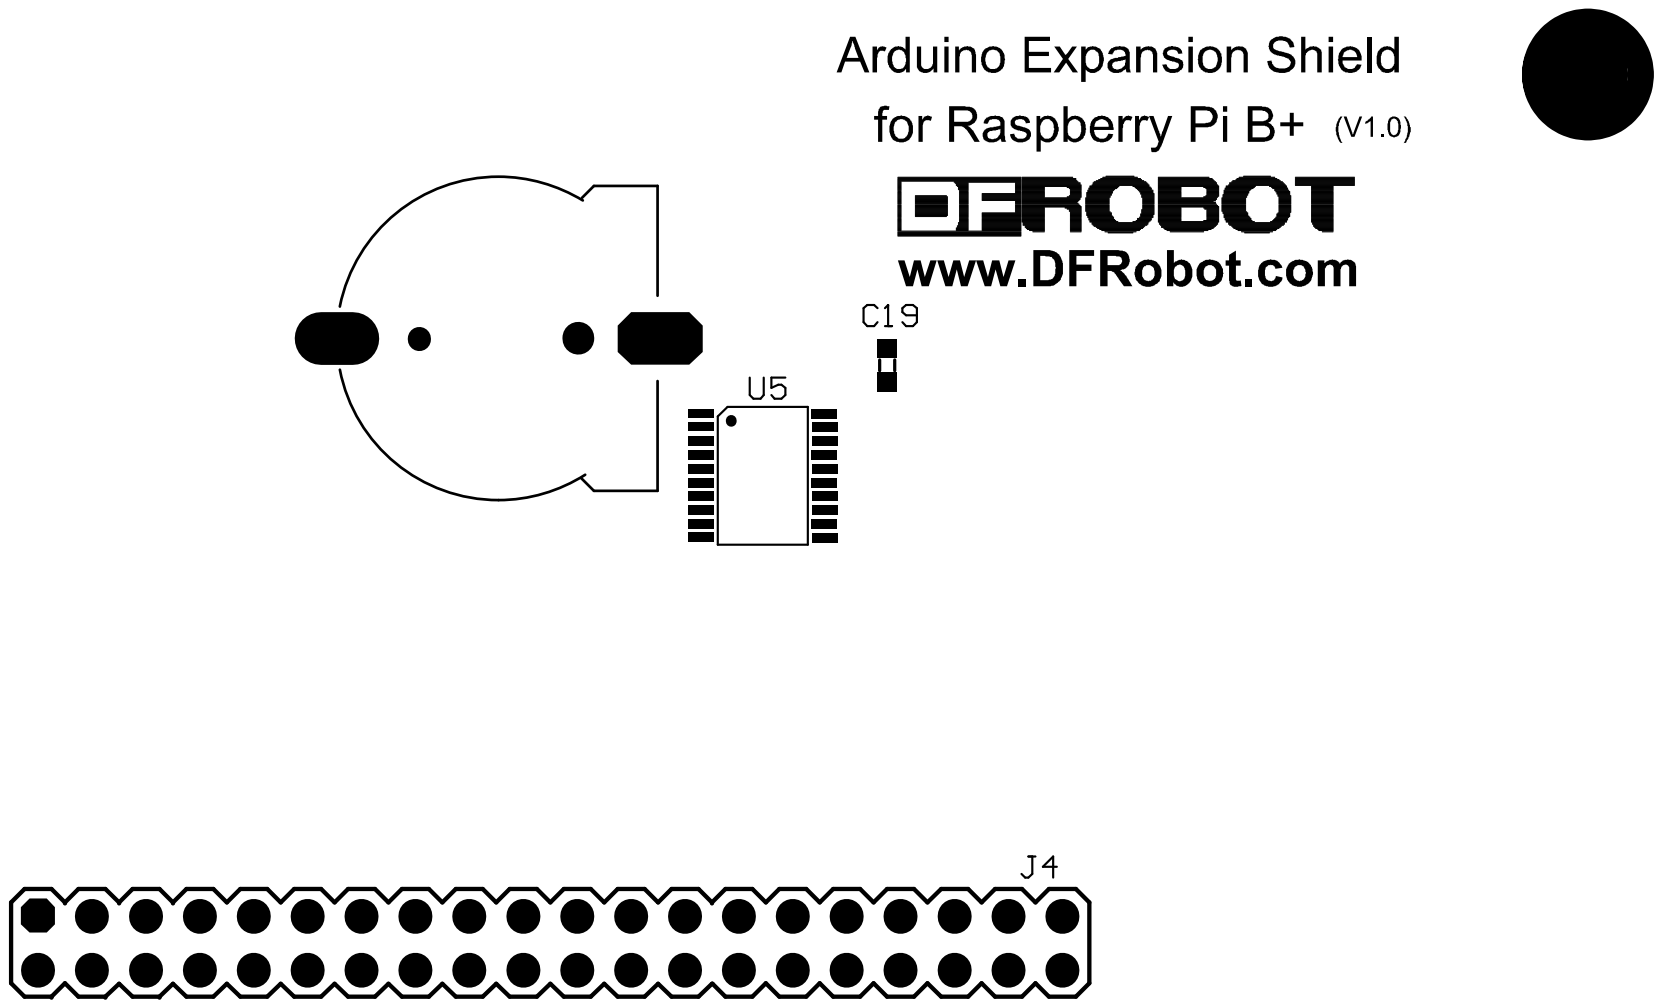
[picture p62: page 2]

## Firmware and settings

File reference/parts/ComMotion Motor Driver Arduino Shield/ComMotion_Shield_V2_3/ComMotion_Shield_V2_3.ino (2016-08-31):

#include <EEPROM.h>
#include <Wire.h>
#include "IOpins.h"
#include "Notes.h"

byte mcu;                                                                     // designation as MCU 1 or MCU 2 as determined by state of pin A2
byte address;                                                                 // I²C address based on dipswitches and ID pin

//============================================================================== Motor Control Variables ================================================================================

int acount,bcount;                                                            // encoder pulse counters used to measure distance
volatile byte aflag;                                                          // flag to indicate encoder A has changed state                                                                
volatile byte bflag;                                                          // flag to indicate encoder B has changed state
volatile unsigned long apulse,bpulse;                                         // width of encoder pulses in uS
volatile unsigned long atime,btime;                                           // stores time of last encoder state change
byte motora,motorb;                                                           // values will be 0&1 on MCU1 and 2&3 on MCU2     - precalculated to increase speed
long maxpulse[4];                                                             // max time between encoder state changes in uS   - precalculated to increase speed

//============================================================================== Configuration Data======================================================================================

byte demo;                                                                    // demo mode                   modes : 0 = OFF,  1 = Line,  2 = Object
byte mode=0;                                                                  // default to standby          modes : 0 = standby, 1 = I²C command, 2 = Serial command, 3 = Scamper Demo
byte configuration=0;                                                         // default to Omni 3 wheel     config: 0 = Omni 3 wheel, 1 = Omni 4 wheel, 2 = Mecanum, 3 = Individual
byte lowbat=60;                                                               // low battery voltage (60 = 6.0V)
int maxamps[4];                                                               // used to set maximum current allowed (255 = 2.55A) for each motor
byte master=1;                                                                // external master address (default=1)
byte addroffset=0;                                                            // optional I²C address offset (default=0)
byte defaulted;                                                               // used to determine if defaults need to be loaded
byte encoders;                                                                // flag to indicate if encoder feedback is enabled or disabled
int motrpm[4];                                                                // motor rpm used to determine max speed
int encres[4];                                                                // encoder resolution (x100) used to determine max speed
byte reserve[4];                                                              // reserve power to ensure accurate speed under changing load
long stalltm[4];                                                              // stall time in mS used to determine if a motor is running slow or stalled
byte sermode;                                                                 // serial mode determines where commands come from and data goes to
unsigned int baudrate[2];                                                     // baud rate for each serial port


//============================================================================== Shield Control Variables ===============================================================================

int velocity=0;                                                               // requested speed
int angle=-360;                                                               // requested angle of travel
int rotation=0;                                                               // requested rotation
int mspeed[4];                                                                // requested speed of individual motors

float radconvert=PI/180;                                                      // used to convert radians into degrees (precalculated to improve speed)

byte analogpin[5]={0,1,3,6,7};                                                // analog inputs to scan: A0=current A, A1=current B, A3 & A6=spare, A7=voltage on MCU1 or spare / sensor on MCU2
int  analogvalue[5];                                                          // store analog input results
byte datapack[32];                                                            // command/config data packet
byte sendpack[32];                                                            // data send packet for returning status data
byte serpack[36];                                                             // serial data pack
byte syncpack=1;                                                              // sync pack type (default: 1=controller config) 
byte packsize;                                                                // size of command packet    
byte command=255;                                                             // 255 = no command 
byte analog;                                                                  // read different analog input each loop (analog conversion takes 260uS)
byte powerdown=0;                                                             // a value of 1 shuts down all motors to conserve power and prevent a brownout condition

int  voltage;                                                                 // battery voltage
byte eflag=0;                                                                 // error flag records faults such as over current and under voltage
byte i2cfreq=1;                                                               // default value for I²C

//============================================================================== Demo global variables ==================================================================================

unsigned long time=millis();
unsigned long IRtime=millis();

void setup()
{
  //============================================================================ Use Reset Button to select demo mode ===================================================================
  
  EEPROMload();                                                               // load configuration from EEPROM
  if(defaulted!=170) EEPROMdefaults();                                        // load defaults if no previous configuration found or in demo mode
  
  for(byte i=0;i<4;i++)
  {
    maxpulse[i]=60000000L/(long(motrpm[i])*long(encres[i])/100L)*255L;
    maxpulse[i]=maxpulse[i]*(100L-long(reserve[i]))/100L;
  }
  
  DDRD=B00000011;                                                             // ensure dipswitch pins (PD4-PD7) and encoder inputs (PD2,PD3) plus RX and TX are set to input
  PORTD=PORTD|B11111100;                                                      // enable pullup resistors on dipswitch pins (PD4-PD7) and encoder inputs (PD2,PD3)
  DDRB=DDRB|B00001111;                                                        // set motor control pins PB0 - PB3 (D8,D9,D10,D11) as output
  

  mcu=digitalRead(IDpin);                                                     // low = MCU 1    high = MCU 2
  address=((PIND&B11110000)>>3)+addroffset+mcu;                               // I²C address is selected by dip switches + offset + state of ID pin (MCU1 or MCU2).
  motora=mcu*2;
  motorb=mcu*2+1;
  
  Wire.begin(address);                                                        // initialize I²C library and set slave address
  Wire.onReceive(I2C_Receive);                                                // define I²C slave receiver ISR
  Wire.onRequest(I2C_Send);                                                   // define I²C slave transmit ISR
  Wire.setTimeout(1L);                                                        // sets a timeout of 1mS for I²C
  Wire.flush();
  delay(100);                                                                 // required to ensure both processors are initialized before inter-communications begins
    
  if(i2cfreq==0)                                                              // thanks to Nick Gammon: http://gammon.com.au/i2c
  {
    TWBR=72;                                                                  // default I²C clock is 100kHz
  }
  else
  {
    TWBR=12;                                                                  // change the I²C clock to 400kHz
  }
  
  if(mode==1 && mcu==0)                                                       // if demo mode is selected
  {
    demo+=1;                                                                  // toggle demo every time power is turned on or reset is pressed
    if(demo>1) demo=0;                                                        // limit demo to 0, 1 or 2
    
    angle=0;
    
    EEPROM.write(0,demo);                                                     // update demo mode
    
    Wire.beginTransmission(address+1);
    datapack[0]=15;                                                           // command 15 used to syncronize demo mode 
    datapack[1]=demo;
    datapack[2]=mode;
    Wire.write(datapack,3);
    Wire.endTransmission();
  }
  else
  {
    delay(10);
  }

  Serial.begin(long(baudrate[mcu]));                                          // initialize Serial library and set baud rate
  Serial.setTimeout(1L);                                                      // sets a timeout of 1mS for Serial. Baud below 9600 should not be used unless this value is increased
  
  //if(mcu) TXconfig();
  delay(1);
  
  while(millis()-time<1000)
  {
  }
  
  if(mode)                                                                    // if the shield is in demo mode
  {
    if(demo==0) Beep(3);
    if(demo==1) Tune();                                                       // Demo mode - play "Row, row, row your boat" using the motors for speakers
    if(demo==2) Beep(5);
  }
  
  //============================================================================ Encoder Interrupts =====================================================================================

  attachInterrupt(0,Aencoder,CHANGE);                                         // call ISR for left  encoder when state changes
  attachInterrupt(1,Bencoder,CHANGE);                                         // call ISR for right encoder when state changes
}


void loop()
{ 
  //---------------------------------------------------------------------------- Read analog inputs including battery voltage and motor currents ----------------------------------------
  analog++;                                                                   // select a different input each loop (analog read takes 260uS)
  if(analog>4) analog=0;                                                      // rotate through current A, current B, A3, A6 and A7
  
  if(mode && demo>0)
  {
    if(demo==1) LineFollow();
    if(demo==2) Avoidance();
    Motors();
    return;
  }
  
  analogvalue[analog]=analogRead(analogpin[analog]);                          // read selected analog input and store in array for later retrieval
  if(mcu==0 && analog==4) voltage=analogvalue[4]*30/185;                      // convert to battery voltage (60 = 6.0V)
  
  //---------------------------------------------------------------------------- Shut down motors if battery is equal or below lowbat ---------------------------------------------------

  if(mcu==0 && analog==4 && powerdown<250)                                    // battery voltage has just been read and no powerdown has occured
  {
    if(analogvalue[4]<=lowbat)                                                // compare battery voltage to low battery voltage
    {
      eflag=eflag|B00010000;                                                  // bit 5 indicates power dipping below batlow voltage
      powerdown++;                                                            // increment shutdown counter if battery voltage is low
    }
    else
    {
      powerdown=0;                                                            // reset shutdown counter if battery voltage is high
    }
    if(powerdown>249) PowerDown();                                            // if battery voltage consistantly low for 250 samples shutdown all motors
  }
  if(powerdown>249) return;                                                   // power must be cycled or reset button pressed to resume
  
  //---------------------------------------------------------------------------- Shield Functions ---------------------------------------------------------------------------------------
  
     
  if(Serial.available()>0) SerialInput();                                     // receive and transfer serial data depending on serial mode
  if(command<32) Commands();                                                  // respond to command from I²C bus or Serial interface
  if(encoders)
  {
    Motors();                                                                 // if encoders are enabled then use then to control motor speeds
  }
  else                                                                        // if encoders are disabled then feed speed values directly to PWM output
  {                                                                            
    analogWrite(pwmapin,abs(mspeed[mcu*2]));                                  // set motor A speed
    digitalWrite(dirapin,mspeed[mcu*2]>0);                                    // set motor A direction
    analogWrite(pwmbpin,abs(mspeed[mcu*2+1]));                                // set motor B speed
    digitalWrite(dirapin,mspeed[mcu*2+1]>0);                                  // set motor B direction
  }
}

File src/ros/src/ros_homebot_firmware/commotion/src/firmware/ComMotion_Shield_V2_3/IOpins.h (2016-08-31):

#define encapin     2    // D02 PD2 (INT0) - Motor A encoder   sensor  pin
#define encbpin     3    // D03 PD3 (INT1) - Motor B encoder   sensor  pin
#define dirapin     8    // D08 PB0 (ICP1) - Motor A direction control pin
#define pwmapin     9    // D09 PB1 (OC1A) - Motor A speed     control pin
#define pwmbpin    10    // D10 PB2 (OC1B) - Motor B speed     control pin
#define dirbpin    11    // D11 PB3 (OC1C) - Motor B direction control pin
#define IDpin      16    // D16 PC2 (ADC2) - MCU     identification    pin      LOW=MCU1  HIGH=MCU2

#define curapin     0    //  A0 PC0 (ADC0) - Motor A current   sensor  pin
#define curbpin     1    //  A1 PC1 (ADC1) - Motor B current   sensor  pin
#define voltpin     7    //  A7     (ADC7) - Voltage on MCU1
#define senspin     7    //  A7     (ADC7) - Sensor  on MCU2
#define irpin      17

// ™©®°±€£¢¥ º¹²³ ¼½¾÷Ω∞≈≠√∑πµΔπ

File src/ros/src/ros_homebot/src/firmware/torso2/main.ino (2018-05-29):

/*
 * Copyright 2017 Chris Spencer
 */
// http://wiki.ros.org/rosserial_arduino/Tutorials/Hello%20World
//#include "Arduino.h"
#include <ros.h>
#include <math.h>
#include <stdint.h>
#include <tf/tf.h>
#include <tf/transform_broadcaster.h>
#include <geometry_msgs/Quaternion.h>
#include <std_msgs/Empty.h>
#include <std_msgs/Bool.h>
#include <std_msgs/Byte.h>
#include <std_msgs/Int16.h>
#include <std_msgs/Int64.h>
#include <std_msgs/Float32.h>
#include <std_msgs/Float32MultiArray.h>
#include <std_msgs/Int32MultiArray.h>
#include <std_msgs/Int16MultiArray.h>
#include <std_msgs/Int8MultiArray.h>
#include <std_msgs/UInt16MultiArray.h>
#include <std_msgs/String.h>
#include <sensor_msgs/Range.h>
#include <sensor_msgs/BatteryState.h>
#include <sensor_msgs/Imu.h>
#include <geometry_msgs/Twist.h>
#include <nav_msgs/Odometry.h>
//#include <diagnostic_msgs/DiagnosticArray.h>
#include <diagnostic_msgs/DiagnosticStatus.h>
//#include <diagnostic_msgs/KeyValue.h>
#include <Wire.h>
#include <MemoryFree.h>

#include "ArduinoPinout.h"
#include "I2CAddresses.h"
#include "BooleanSensor.h"
#include "BatteryVoltageSensor.h"
#include "MotionController.h"
#include "UltrasonicSensor.h"
#include "AccelGyroSensor.h"
#include "PowerController.h"
#include "ArduinoTemperatureSensor.h"
#include "AnalogSensor.h"
#include "OdometryTracker.h"
#include "EEPROMAnything.h"

//#define PING_TIMEOUT_MS 10000

#define DIAGNOSTIC_STATUS_LENGTH 1
#define DIAGNOSTIC_REPORT_FREQ_MS 1000 // 1 seconds
//#define DIAGNOSTIC_REPORT_FREQ_MS 10000 // 10 seconds

#define HEALTHY_BLINK_PERIOD 3000
#define DISCONNECTED_BLINK_PERIOD 250

// The time it spends moving backwards trying to detach from the dock coupling before giving up.
#define UNDOCKING_START_TIMEOUT_MS 3000

// The time it spends moving backwards after detaching from the dock coupling to clear the docking station.
#define UNDOCKING_CLEAR_TIMEOUT_MS 1000

// Debug levels.
#define ONLY_ERRORS 0 // default
#define UP_TO_OK 1

// Persistent variables.
struct config_t {
    bool imu_saved;
    //adafruit_bno055_offsets_t imu_calib;
    uint16_t accel_offset_x;
    uint16_t accel_offset_y;
    uint16_t accel_offset_z;
    uint16_t gyro_offset_x;
    uint16_t gyro_offset_y;
    uint16_t gyro_offset_z;
    uint16_t mag_offset_x;
    uint16_t mag_offset_y;
    uint16_t mag_offset_z;
    uint16_t accel_radius;
    uint16_t mag_radius;
} configuration;

char base_link[] = "/base_link";
const char * const ultrasonic_links[] = { "/base_link/ultrasonic0", "/base_link/ultrasonic1", "/base_link/ultrasonic2" };
char odom_link[] = "/odom";

unsigned long blink_period = DISCONNECTED_BLINK_PERIOD;
unsigned long last_blink = 0;

// Convert the BNO055's calibration code [0-3] to a diagnostics status.
int calib_to_status[] = {
    diagnostic_msgs::DiagnosticStatus::ERROR, //2, raw 0=uncalibrated
    diagnostic_msgs::DiagnosticStatus::WARN,  //1, raw 1=partial
    diagnostic_msgs::DiagnosticStatus::WARN,  //1, raw 2=almost
    diagnostic_msgs::DiagnosticStatus::OK     //0, raw 3=completely calibrated
};

AccelGyroSensor ag_sensor = AccelGyroSensor();

MotionController motion_controller;

OdometryTracker odometry_tracker = OdometryTracker();

//geometry_msgs::TransformStamped ts;
//tf::TransformBroadcaster tf_broadcaster;
//tf::Transform transform;
//tf::TransformBroadcaster br;
//tf::Transform transform;

// If true, ultrasonic sensors will be read and reported.
bool ultrasonics_enabled = false;

// Space each reading to prevent echo from interfering with sequential readings.
int ultrasonics_spacing = 10;

// If set to true, all motors will be stopped immediately.
bool halt = false;

// If true, all sensors will push their current readings to the host, even if they haven't changed
// since last polling.
bool force_sensors = false;
bool noticed_force_sensors = false;

// Records when we last received a message from rosserial on the host.
// This is used to detect a lost connection to the host and perform emergency shutdown of the motors.
bool connected = false;

// http://wiki.ros.org/roscpp/Overview/Logging
// http://wiki.ros.org/rosserial/Overview/Logging
ros::NodeHandle nh;

//http://wiki.ros.org/std_msgs
//http://wiki.ros.org/common_msgs
std_msgs::Int16 int16_msg;
std_msgs::Byte byte_msg;
std_msgs::Bool bool_msg;
std_msgs::Float32 float_msg;
std_msgs::String string_msg;
std_msgs::UInt16MultiArray uint16ma_msg;
sensor_msgs::Range range_msg;
sensor_msgs::BatteryState battery_msg;
sensor_msgs::Imu imu_msg;
geometry_msgs::Vector3 vec3_msg;
nav_msgs::Odometry odom_msg;

unsigned long last_imu_auto_load_time = 0;

// Array representation of adafruit_bno055_offsets_t.
//uint16_t imu_calibration_array[11] = {0};
adafruit_bno055_offsets_t imu_calib_struct;

#define MAX_OUT_CHARS 255
#define TEN_CHARS 10
char buffer[MAX_OUT_CHARS + 1];  //buffer used to format a line (+1 is for trailing 0)
char midbuffer[TEN_CHARS + 1];  //buffer used to format a line (+1 is for trailing 0)
char prebuffer[TEN_CHARS + 1];  //buffer used to format a line (+1 is for trailing 0)

bool battery_changed = false;

unsigned long cnt = 0;
unsigned long last_debug = 0;

bool report_diagnostics = false;
unsigned long last_diagnostic = 0;

unsigned long a_encoder_last_change = 0;
unsigned long b_encoder_last_change = 0;

int general_status = diagnostic_msgs::DiagnosticStatus::OK;

// If false, stays on when it becomes disconneced.
// If set to false, then if we lose connection to the host, we power off.
bool deadman = false;

// Flags to track when the IMU first becomes ready.
// We track this separately from the IMU's direct flags, because those can turn false, as the fusion algorithm constantly recalibrates.
// When this happens, the IMU will read uncalibrated, even though it's still generating usable euler angles and other motion data,
// so we don't want treat this as an error condition.
int accel_ready, gyro_ready, magnetometer_ready, imu_ready;

//diagnostic_msgs::DiagnosticArray dia_array;
//diagnostic_msgs::DiagnosticStatus robot_status;
//diagnostic_msgs::KeyValue status_keyvalue;

//https://learn.adafruit.com/memories-of-an-arduino/measuring-free-memory
//int freeRam ()
//{
//  extern int __heap_start, *__brkval;
//  int v;
//  return (int) &v - (__brkval == 0 ? (int) &__heap_start : (int) __brkval);
//}

/*
 * Begin sensor definitions.
 */

BatteryVoltageSensor battery_voltage_sensor = BatteryVoltageSensor(
    // The battery consists of 3 * 4.2V lipo cells.
    12.6,
    2000000, // ohms
    1000000, // ohms
    BATTERY_VOLTAGE_PIN,
    // dead_ratio, The battery is considered dead when 80% discharged.
    0.8,
    // voltage_offset, 10.9 measured by the Arduino's ADC is really 11.9 as measured by a good multimeter.
    2
);
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

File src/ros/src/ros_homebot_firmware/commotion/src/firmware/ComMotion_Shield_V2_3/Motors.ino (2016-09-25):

void Motors()
{
  //============================================================================ Motor Speed Control ====================================================================================

  unsigned long actual;                                                       // temporary calculation of desired speed in uS per encoder pulse
  static byte apwm,bpwm;                                                      // A and B motor speeds
  static byte astall,bstall;                                                  // flags to indicate a stalled motor

  if(aflag==1 || astall==1)                                                   // if encoder A has changed states or motor A has stalled                  
  {
    apulse=(micros()-atime);                                                  // time between last state change and this state change
    atime=micros();                                                           // update atime with time of most recent state change
    actual=maxpulse[motora]/abs(mspeed[motora]);                              // calculate desired time in uS between encoder pulses
    if(actual>apulse && apwm>0) apwm--;                                       // if motor is running too fast then decrease PWM
    if(actual<apulse && apwm<255) apwm++;                                     // if motor is running too slow then increase PWM
    if(mspeed[motora]==0) apwm=0;                                             // override speed adjust if speed is 0 for quick stop
    analogWrite(pwmapin,apwm);                                                // update motor speed
    digitalWrite(dirapin,mspeed[motora]>0);                                   // set direction of motor
    astall=0;                                                                 // reset stall flag
    aflag=0;                                                                  // reset encoder flag
  }

  if(bflag==1 || bstall==1)                                                   // if encoder B has changed states or motor B has stalled  
  {  
    bpulse=(micros()-btime);                                                  // time between last state change and this state change
    btime=micros();                                                           // update btime with time of most recent state change
    actual=maxpulse[motorb]/abs(mspeed[motorb]);                              // calculate desired time in uS between encoder pulses
    if(actual>bpulse && bpwm>0) bpwm--;                                       // if motor is running too fast then decrease PWM
    if(actual<bpulse && bpwm<255) bpwm++;                                     // if motor is running too slow then increase PWM
    if(mspeed[motorb]==0) bpwm=0;                                             // override speed adjust if speed is 0 for quick stop
    analogWrite(pwmbpin,bpwm);                                                // update motor speed
    digitalWrite(dirbpin,mspeed[motorb]>0);                                   // set direction of motor
    bstall=0;                                                                 // reset stall flag
    bflag=0;                                                                  // reset encoder flag
  }  
  
  

  //============================================================================ Check for stalled motors ===============================================================================

  if(analogvalue[0]>maxamps[motora])                                          // motor A maximum current exceeded
  {
    apwm=apwm/2;                                                              // halve pwm
    if(mcu==0) eflag=eflag|COMMOTION_ERROR_M1_MAXCURRENT;                     // bit 0 indicates M1 has exceeded current limit
    if(mcu==1) eflag=eflag|COMMOTION_ERROR_M3_MAXCURRENT;                     // bit 2 indicates M3 has exceeded current limit
  }

  if(mspeed[motora]==0)                                                       // if motor A speed is supposed to be 0 or motor current exceeds limit
  {
    apwm=0;                                                                   // ensure apwm=0
    analogWrite(pwmapin,apwm);                                                // cut power to motor A
  }
  else
  {
    if(micros()-atime>(stalltm[motora]*1000L))                                // if encoder A has not changed states within 10mS
    {
      astall=1;                                                               // set motor A stall flag
      apwm+=2;                                                                // jump start apwm value
      if(apwm>253) apwm=253;
    }
  }

  if(analogvalue[1]>maxamps[motorb])                                          // motor B maximum current exceeded
  {
    bpwm=bpwm/2;                                                              // halve pwm
    if(mcu==0) eflag=eflag|COMMOTION_ERROR_M2_MAXCURRENT;                     // bit 1 indicates M2 has exceeded current limit
    if(mcu==1) eflag=eflag|COMMOTION_ERROR_M4_MAXCURRENT;                     // bit 3 indicates M4 has exceeded current limit
  }

  if(mspeed[motorb]==0)                                                       // if motor B speed is supposed to be 0 or motor current exceeds limit
  {
    bpwm=0;                                                                   // ensure bpwm=0
    analogWrite(pwmbpin,bpwm);                                                // cut power to motor B
  }
  else
  {
    if(micros()-btime>(stalltm[motorb]*1000L))                                // if encoder B has not changed states within 10mS 
    {
      bstall=1;                                                               // set motor B stall flag
      bpwm+=2;                                                                // jump start bpwm value
      if(bpwm>253) bpwm=253;
    }
  }
}


//============================================================================== Encoder ISRs =================================================================

void Aencoder()                                                               // left  encoder Interrupt Service Routine
{
  aflag = 1;                                                                    // set flag for left  encoder
  
//  acount += 1;//ok
//  acount = mspeed[motora];//ok
//  acount += mspeed[motora] > 0;//ok
//  acount = mspeed[motora] < 0;//ok
//  acount = mspeed[motora] > 0;//ok
//  acount += mspeed[motora] < 0;//ok
//  acount = -1;//ok
//  acount = mdir[motora];//bad
//  acount += mdir[motora];
  //acount += (mspeed[motora]>0)-(mspeed[motora]<0);
  if(mspeed[motora] > 0){
    acount += 1;
  }else if(mspeed[motora] < 0){
    acount -= 1;
  }
}

void Bencoder()                                                               // right encoder Interrupt Service Routine
{
  bflag = 1;    // set flag for right encoder
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

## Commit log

2016-08-31 Initial commit.
    [2s_lipo_charger.fzz, ArduinoPinout.csv, Arduino_Sensor_Shield.stl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]
2016-09-02 Added mock treads. Added part preview images.
    [layout.scad, mock_tread.scad, mock_tread.stl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]
2016-09-04 Added noise filter to LRF.
2016-09-08 Updated exploded model.
    [exploded.scad, exploded_motor.scad, pololu_drive_motor.scad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]
2016-09-17 Updated docs. Updated rviz model.
    [exploded.scad, homebot.urdf.xacro, slam.ods]
2016-09-18 Updated links in urdf model.
    [homebot.urdf.xacro]
2016-09-18 Added neck link. Fixed joints to be movable in rviz.
    [homebot.urdf.xacro, slam.ods]
2016-09-19 Modified head arduino node to publish joint state messages.
2016-09-19 Refactored urdf model. Modified head node to periodically publish joint states.
    [homebot.urdf.xacro]
2016-09-25 Added restart command. Refactored commotion and arduino code to reliably report encoder states.
    [commotion_switch.scad, commotion_switch.stl, flexiTreads_driver.scad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]
2016-10-04 Switched default config over to Ubuntu.
2016-10-09 Updated tilt servo easing code to use library.
2016-10-09 Fixed xacro warnings.
    [homebot.urdf.xacro]
2016-10-12 Fixed sound. Added sample of working /boot/config.txt for Ubuntu 16.
    [boot_config_ubuntu_1604.txt]
2016-10-12 Updated sample config.txt
    [boot_config_ubuntu_1604.txt]
2016-10-13 Misc ubuntu bug fixes. Added fan model. Began treadmill prototype.
    [fan.scad, head.scad]
2016-10-13 Renamed arduino diagnostics.
2016-10-19 Added qr tracker.
    [head_fan.fzz]
2016-10-22 Refactored node locations. Fixed code formatting.
    [constants.py]
2016-10-23 Added battery pack circuit.
    [battery_pack.fzz]
2016-10-23 Updated battery pack circuit.
    [battery_pack.fzz]
2016-10-24 Updated docs and battery circuits.
    [2s_lipo_charger.fzz]
2016-10-24 Updated imu visualization.
2016-10-25 Fixed IMU message publishing and visualization.
2016-10-30 Updated circuit docs. Fixed bug in Python node.
    [head_fan.fzz]
2016-10-30 Added RPi fan shroud.
    [head_fan_shroud.scad, head_fan_shroud.stl, printing_recommendations.csv]
2016-10-30 Added Pi CPU speed to diagnostics.
    [battery_balance_cable.fzz]
2016-10-31 Added logging to arduino nodes. Decreased reporting of imu packets.
2016-10-31 Added ask error tracking to arduino node.
2016-11-01 Changed arduino node reset to only reset serial connection, not arduino.
2016-11-05 Updated docs and research.
    [batteries.ods, battery-chargers.ods]
2016-12-07 Updated research docs.
    [BatteryCustom.scad, batteries.ods, battery-chargers.ods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]
2016-12-10 Added speech recognition and VAD test examples.
    [battery charging layout.fzz]
2016-12-13 Added odom publishing to torso node.
    [prior-art.ods]
2016-12-25 Improved odometry reporting. Updated research on similar projects.
    [homebot.urdf.xacro, prior-art.ods]
2017-01-09 Improved arduino torso timeout.
2017-01-15 Added led node. Added initial methods to trigger absolute movement.
    [prior-art.ods]
2017-01-16 Added pics. Updated firmware to support discrete movement. Fixed timing bug in torso node.
    [constants.py, main.ino]
2017-02-05 Changed arduino node threads to use full duplex serial.
2017-02-05 Updated torso firmware to not conflict led toggle with power controller.
2017-02-06 Pin mkdocs to latest version 0.16.1
2017-02-06 Pin mkdocs-bootstrap to latest version 0.1.1
2017-02-06 Pin tox to latest version 2.6.0
2017-02-06 Pin pylint to latest version 1.6.5
2017-02-06 Pin cpplint to latest version 1.3.0
2017-02-06 Pin burlap to latest version 0.9.2
2017-02-06 Pin pgi to latest version 0.0.11.1
2017-02-06 Pin catkin-pkg to latest version 0.2.10
2017-02-06 Pin scipy to latest version 0.18.1
2017-02-06 Pin humanize to latest version 0.5.1
2017-02-06 Pin numpy to latest version 1.12.0
2017-02-06 Pin vispy to latest version 0.4.0
2017-02-06 Pin cv2 to latest version 1.0
2017-02-13 Added torso firmware based on rosserial.
    [ArduinoPinout.csv, CPPLINT.cfg]
2017-02-24 Updated torso2 firmware to support basic uno pro.
    [ArduinoUnoProPinout.csv]
2017-03-26 Fixed motion controller in rosserial rewrite. Expanded subscribers.
    [main.ino]
2017-03-26 Fixed formatting.
    [CPPLINT.cfg]
2017-03-27 Fixed formatting. Fixed power controller.
    [main.ino]
2017-03-27 Made torso arduino launch param dynamic.
2017-04-01 Implemented torso arduino ultrasonic range and battery messaging. Added documentation.
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2017-05-29 Refactored torso firmware. Added diagnostics reporting for IMU.
    [ArduinoUnoProPinout.csv]
2017-05-30 Added all torso sensors to diagnostics. Added docs for new neck reference sensor.
    [head.scad, photointerrupter.scad, photointerrupter_OPB940.stl]
2017-06-01 Added imu relay to broad arduino imu data from python node.
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2017-06-04 Completed odoemtry messaging from torso.
    [CPPLINT.cfg, homebot-torso.urdf.xacro]
2017-06-08 Added new head firmware.
    [head.scad, neck_sensor_mount.scad, neck_sensor_mount.stl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]
2017-06-12 Upgraded burlap deploy script and satchels. Refactored Python code.
    [CPPLINT.cfg]
2017-12-07 Misc updates. Added docs and reference material for avr programmer, Rpi, and new photointerruptor part. Removed arduino binary files. Added head arduino rewrite
    [ArduinoPinout.csv, RPi2Pinout.ods, head_arduino_mount.scad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]
2017-12-10 Fixed writeable pins on arduino head.
    [ArduinoPinout.csv]
2017-12-11 Tweaked pan control. Added view camera shortcut.
    [main.ino]
2018-01-17 Added custom logging conf. Fixed massive bug in rosserial causing link to arduinos to fail.
    [ArduinoPinout.csv, ArduinoUnoProPinout.csv]
2018-01-22 Added load to diagnostics. Updated kernel flags, finally fixing arduino pyserial hang. Added true safe poweroff using arduino deadman switch.
    [storage.ods]
2018-02-02 Refactored treads into wheels with casters.
    [bnO055_mount.scad, caster_housing_bottom.scad, caster_housing_bottom.stl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]
2018-02-02 Updated thumbnails.
    [printing_recommendations.csv]
2018-02-22 Fixed head tilt get pin. Updated reporting frequency of torso and head tf and joints data.
    [ArduinoPinout.csv]
2018-03-11 Added 18650 based 3rd generation battery pack. Added recharge dock. Added PID controller for head pan motor.
    [battery.scad, battery_pack.fzz, battery_tray3.scad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]
2018-03-23 Added torso and head motion shortcut commands. Added models for dock masthead. Added initial docking node.
    [computers.ods, dock.scad, dock_masthead.scad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]
2018-05-03 Refactored all arduino topics to not use forward slashes, to work around rostopic msg type bug. Added imu calib save using eeprom to torso arduino firmware.
    [main.ino, torso_motion_server.py]
2018-05-04 Added imu config saving to eeprom. Cleaned up C formatting.
2018-05-18 Removed old serial torso launch files. Updated head and torso firmware to use correct topic names. Improved dock node, added state abstraction.
    [main.ino]
2018-05-29 Fixed motor speed reporting in torso firmware. Added trigger tracking mechanism to state class. Added helper methods to dock node to actuate the different docking approach phases.
    [main.ino]
2018-06-01 Added docking station mast recessor.
    [dock.scad, dock_mast_recessor.scad, dock_mast_recessor.stl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]
2018-06-03 Added improved caster design with shock absorbers.
    [caster_housing_center_bottom.scad, caster_housing_center_bottom.stl, caster_housing_center_top.scad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]
2018-07-06 Updated docking routine. Added link to docking video.
    [prior-art.ods]
